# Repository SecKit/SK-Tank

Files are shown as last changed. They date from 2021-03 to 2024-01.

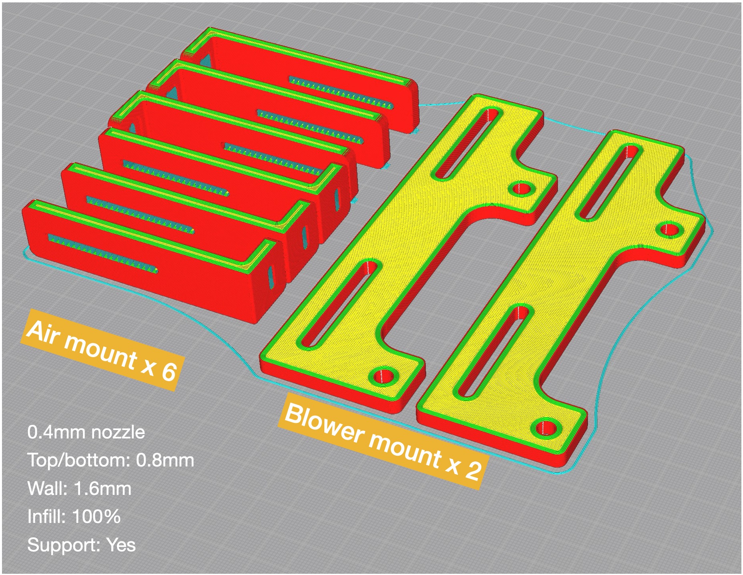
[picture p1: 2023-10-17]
v2/STEP files/must/Side blower ducts/common/slicing tip 1.jpg

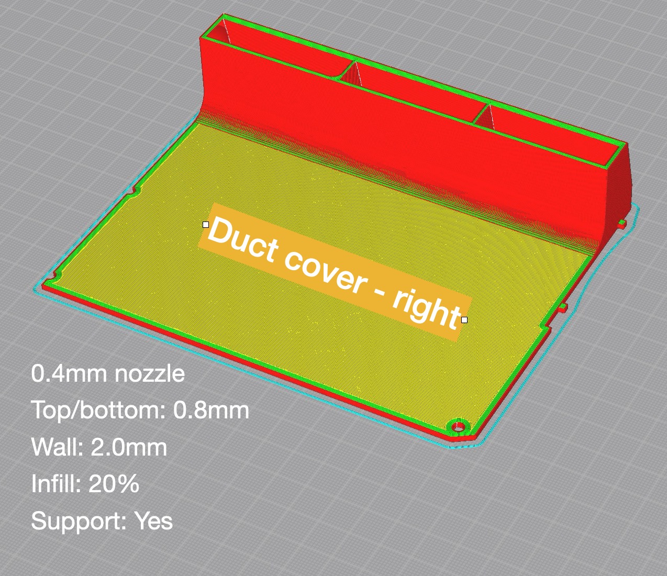
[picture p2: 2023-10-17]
v2/STEP files/must/Side blower ducts/right duct/slicing tip Duct cover - right.jpg

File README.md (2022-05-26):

## SK-Tank All-Metal CoreXY 3D Printer

### Website
https://seckit3dp.design/price/sk-tank

### Wiki: Assembly Manual, tuning guide, etc.
https://sites.google.com/view/seckit-wiki/sk-tank-350x350x400

### Join SecKit's FaceBook group for owner's discussion and latest update
https://www.facebook.com/groups/SecKitCoreXY3DP/

### YouTube
https://www.youtube.com/channel/UCJUHiJfgDE5aeqbk4iZBPHA/videos

### FaceBook Page
https://www.facebook.com/seckit.3dp

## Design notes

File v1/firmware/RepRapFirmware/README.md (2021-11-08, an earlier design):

This firmware pack works on both Mellow Fly CDY v2 and v3 board.

1. Use a max 32G FAT32-format micro SD card. A 64GB or larger card is not supported by Mellow FLY CDY v2 or v3.
2. Extract the zip file and copy all contents in "SK-Tank RRF on Fly CDY v2" directory to the root of a micro SD card.
3. Follow the quick steps in the [Firmware Chapter](https://sites.google.com/view/seckit-wiki/sk-tank-350x350x400/assembly-manual/sk-tank-assembly-manual/12-firmware) of [SK-Tank Assembly Manual](https://sites.google.com/view/seckit-wiki/sk-tank-350x350x400/assembly-manual/sk-tank-assembly-manual) to flash the firmware to your Mellow Fly CDY v2 or v3 control board.

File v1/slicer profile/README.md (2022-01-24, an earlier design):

Thank the community for contributing their settings, but some adjustments can be expected to meet your requirement 😄

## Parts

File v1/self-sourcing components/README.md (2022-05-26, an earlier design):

Self-sourcing components for SK-Tank Barebones Kit.

|Category  |Item | #|Electrical req. |Mechanical req. |
|---|:---|-:|:---|:---|
|Power |Meanwell LRS-200-24 PSU | 1|200 or 350 watt, 24V output |4 holes on back panel (PS.)|
|Power |SSR DC-AC | 1|At least 10 amp AC |2 holes on back panel |
|Power |FS-101 fuse box and fuse | 1|6A for 110V. 3A for 220V. |1 hole on back panel |
|Power |Power switch | 1| | |
|Power |Power cord | 1|At least 0.75 mm^2 internal wire |150cm or longer |
|Control |BigTreeTech Octopus or GTR | 1|At least 6 driver slots |4 holes on back panel |
|Control |TMC2225 | 6|(or other drivers) | |
|Stepper |NEMA17 1.8°/0.9° stepper for XY | 2|Common NEMA 17 stepper | |
|Stepper |NEMA17 1.8° pancake stepper for E | 1|Common NEMA 17 pancake stepper |(PPS.) |
|Extruder  |BMG or Hemera extruder | 1|(PPS.) | |
|Fan |4010 fan for driver cooling | 1|24V | |
|Fan |4020 blower for part cooling | 1|24V | |
|Sensor |Lerdge optical endstop | 3|5V | |
|Sensor |Filament runout sensor | 1|(optional) | |
|Accessory |PTFE tube 3mm ID, 80cm | 1| | |
|Accessory |Cable tie |20| | |
|Accessory |Cable management nylon sleeve, wrapper, etc.| 1| | |

PS. Pre-drilled holes are there on the ACM (Aluminum Composite Material) back panel but you can still drill customized holes easily.

PPS. Use your preferred extruder and design a customized adapter based on [SK-Tank BMG adapter STEP file](https://github.com/SecKit/SK-Tank/tree/master/STEP%20files/extruder%20adapter%20-%20BMG) and [SK-Tank extruder carriage STEP file](https://github.com/SecKit/SK-Tank/tree/master/STEP%20files/extruder%20carriage).

*SecKit will not be responsible for your self-sourcing items.*

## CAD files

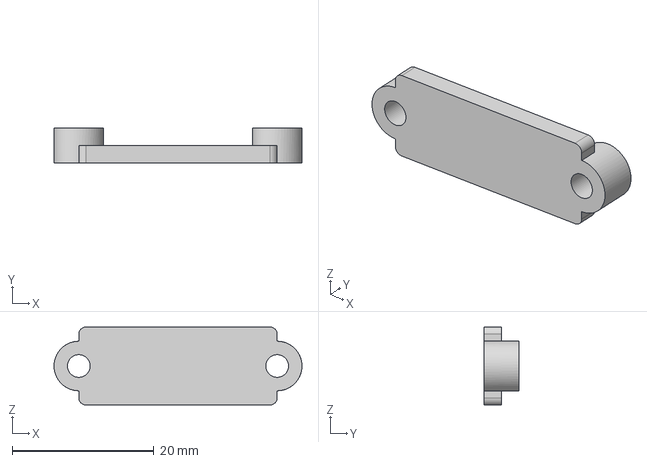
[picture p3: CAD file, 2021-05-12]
STEP files/1. must/Y endstop/Y endstop base.step
35.0 x 5.00 x 11.0 mm

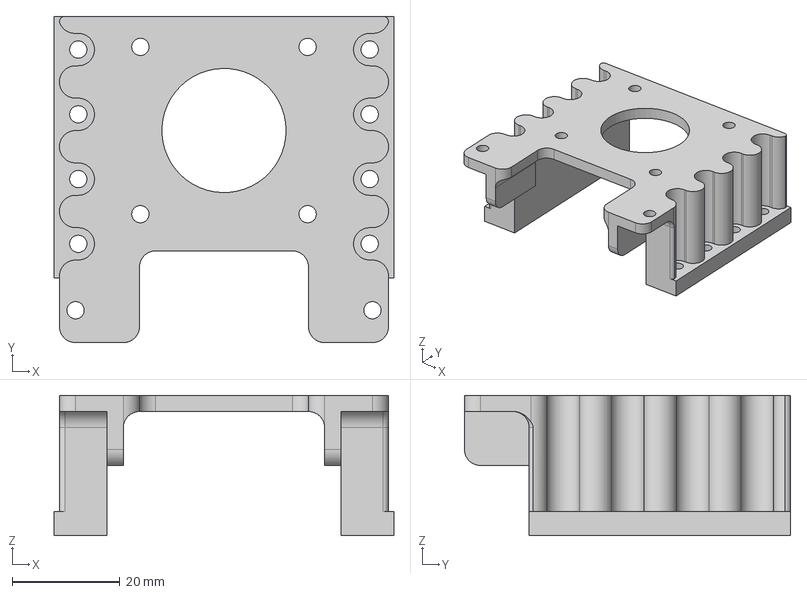
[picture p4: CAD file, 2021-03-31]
STEP files/2. reference/extruder adapter - BMG/SK-Tank BMG printed adapter.step
63.0 x 60.5 x 26.0 mm

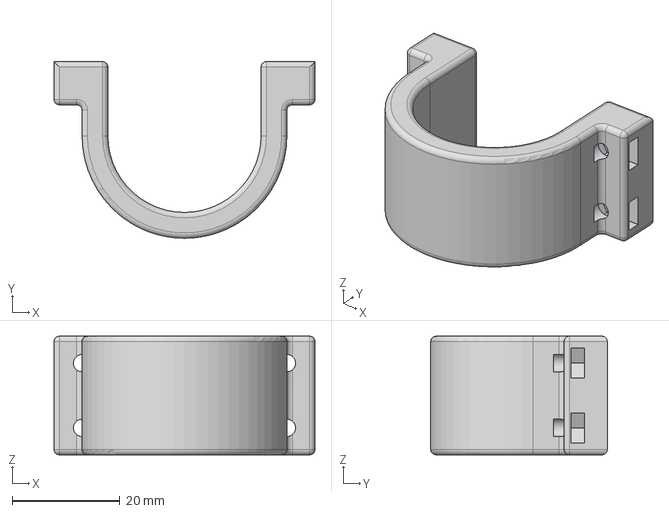
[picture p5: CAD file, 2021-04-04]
STEP files/Belted-Z stepper holder/NEMA8 gearbox bracket.step
48.4 x 32.8 x 22.0 mm

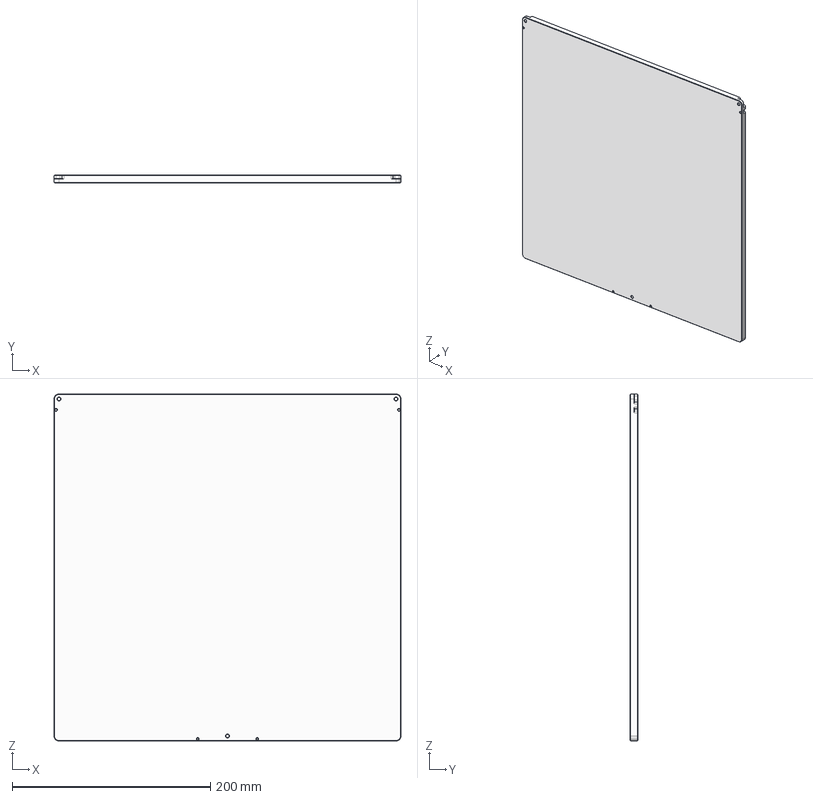
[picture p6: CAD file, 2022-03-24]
STEP files/reference/bed/SK-Tank bed.step
350.0 x 8.00 x 350.0 mm

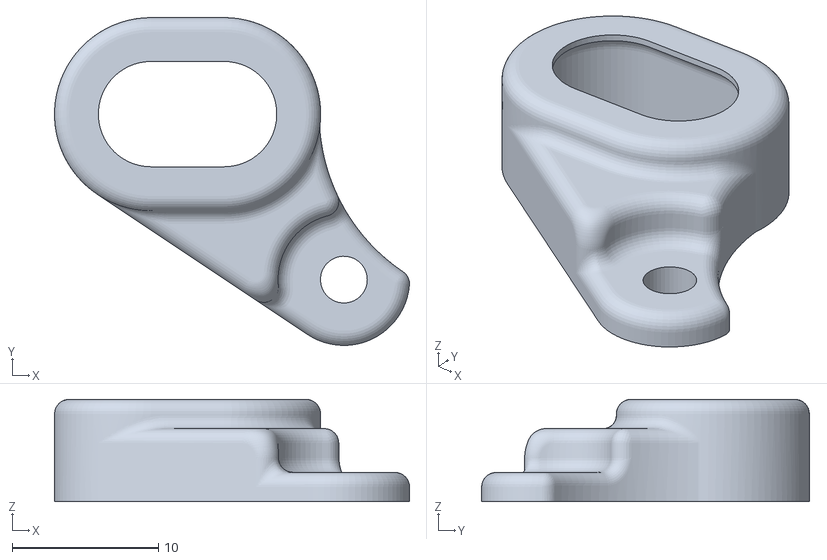
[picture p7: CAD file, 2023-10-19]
v2/STEP files/must/Bed leg guards/right leg guard.stl
24.3 x 22.4 x 7.00

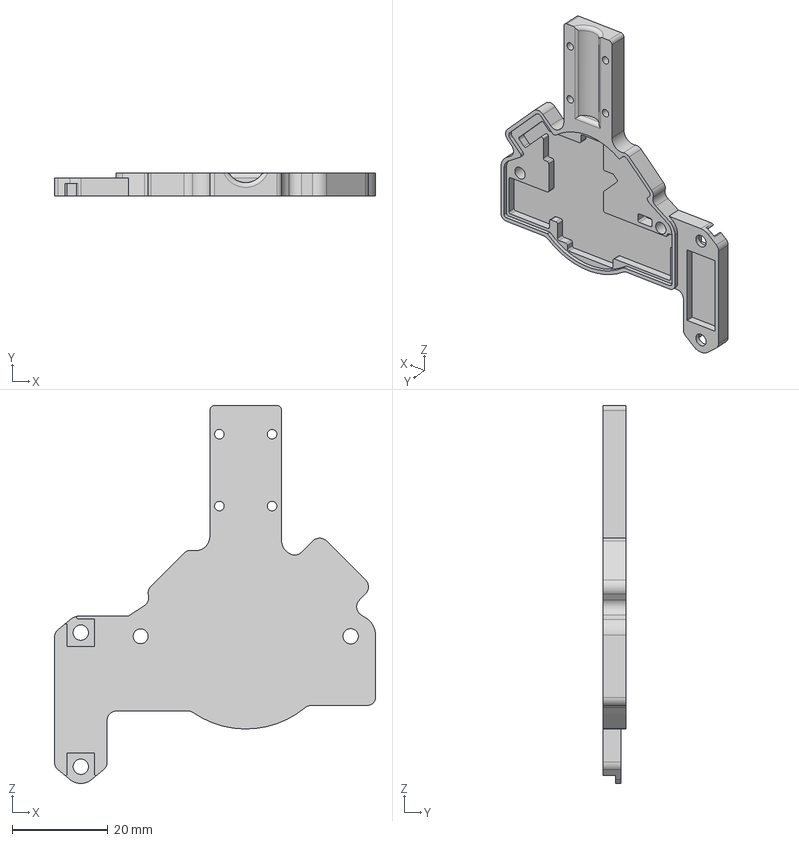
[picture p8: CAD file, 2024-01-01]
v2/STEP files/must/DAB/EBB36 mount/DAB EBB36 mount.step
67.0 x 4.80 x 78.9 mm

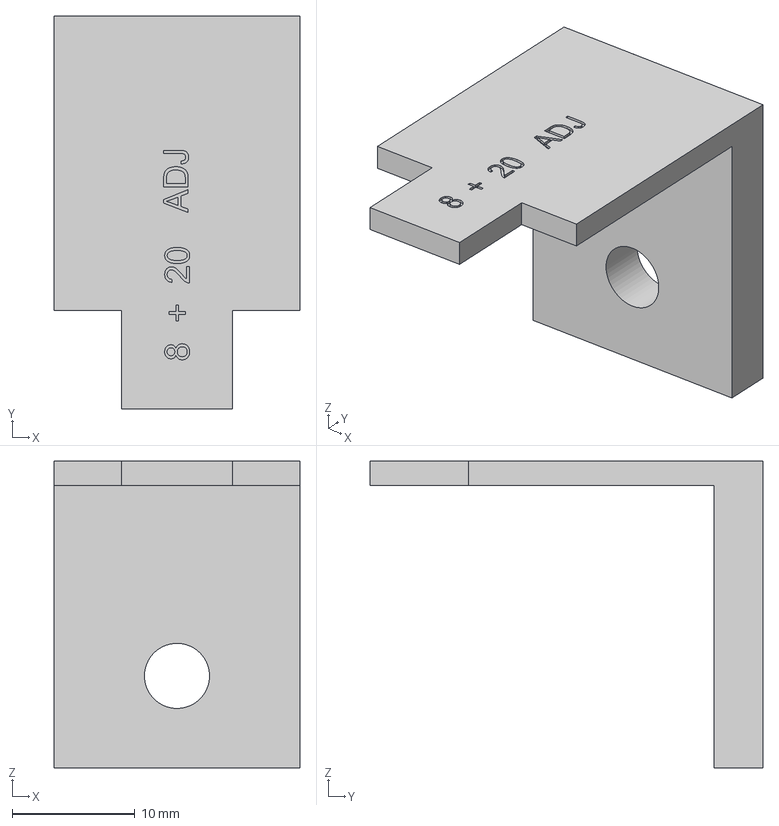
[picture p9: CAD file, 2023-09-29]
v2/STEP files/must/DAB/Fork/DAB fork 8+20 for adjustment.step
20.0 x 32.0 x 25.0 mm

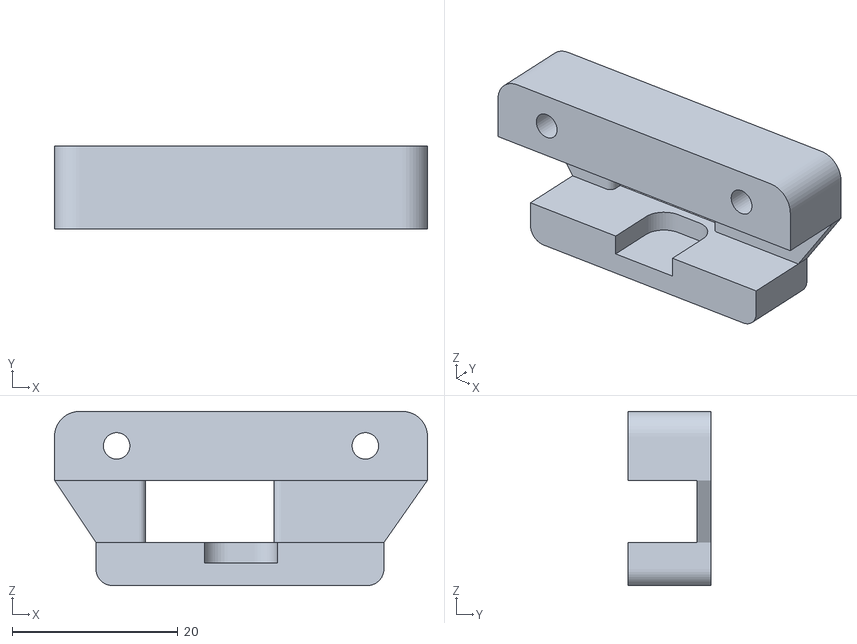
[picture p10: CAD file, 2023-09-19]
v2/STEP files/must/DAB/Latch housing/For MGN12C X linear block/DAB latch housing MGN12C.stl
45.0 x 10.0 x 21.0

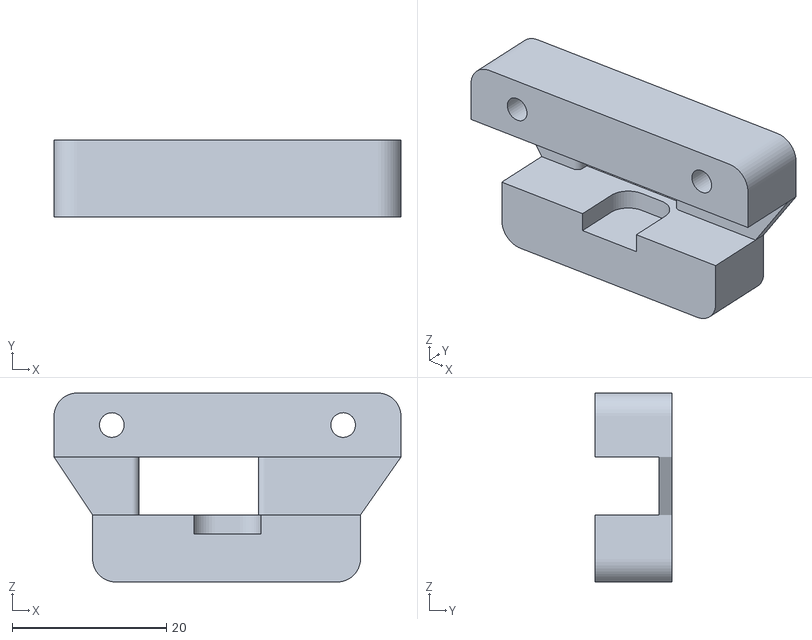
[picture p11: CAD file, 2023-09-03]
v2/STEP files/must/DAB/Latch housing/For MGN9H X linear block/DAB latch housing MGN9H.stl
45.0 x 10.0 x 24.5

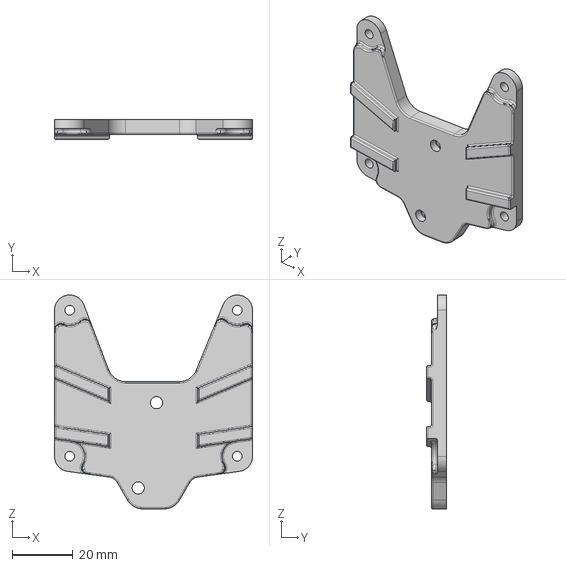
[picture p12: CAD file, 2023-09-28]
v2/STEP files/must/DAB/TBG Air extruder mount/DAB TBG Air extruder mount.step
65.0 x 6.60 x 70.2 mm

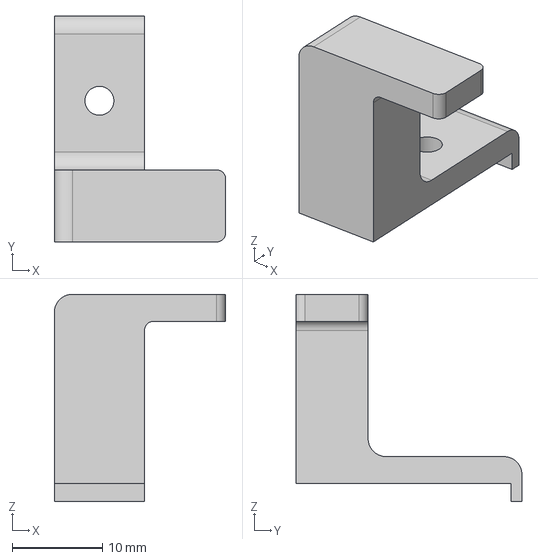
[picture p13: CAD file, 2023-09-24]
v2/STEP files/must/DAB/X endstop finger/DAB X endstop finger.step
19.0 x 25.1 x 23.0 mm

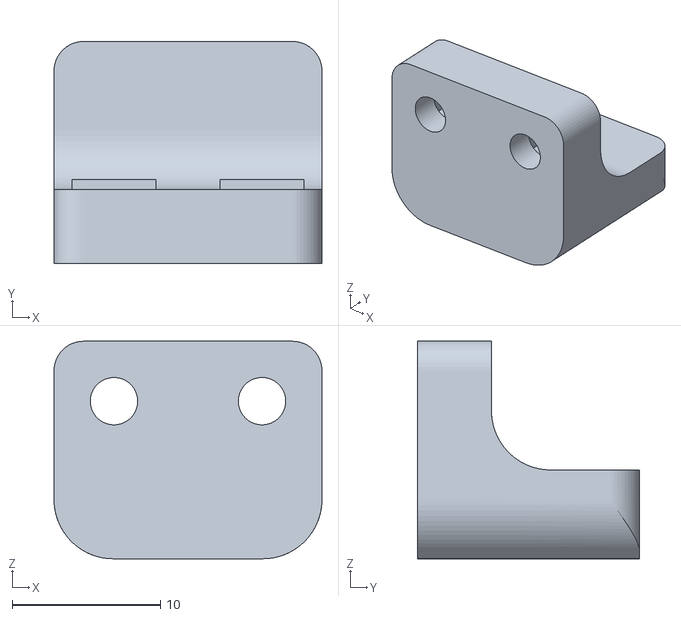
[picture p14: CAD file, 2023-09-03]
v2/STEP files/must/DAB/Z endstop finger/DAB endstop finger.stl
18.1 x 15.0 x 14.7

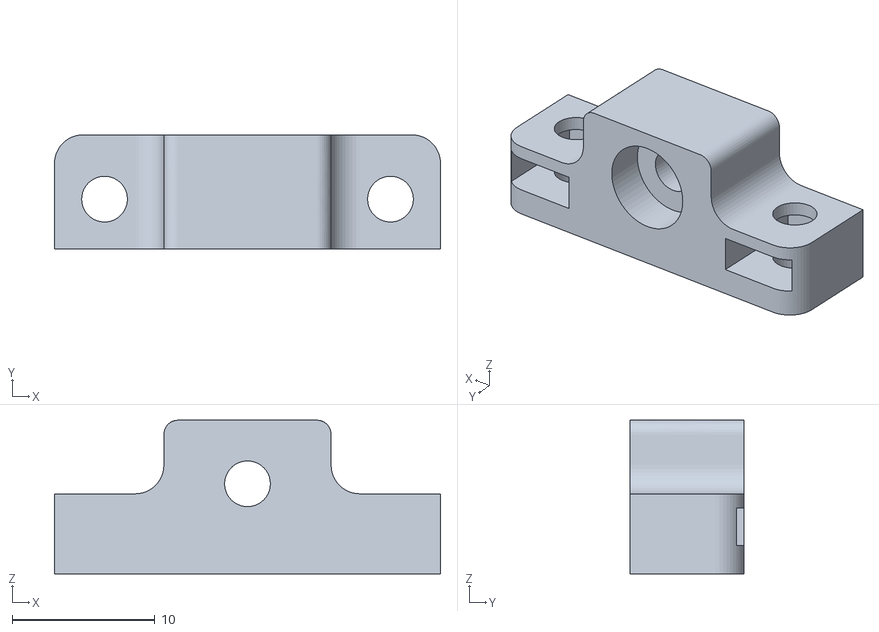
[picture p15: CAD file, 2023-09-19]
v2/STEP files/must/DAB/Z endstop mount/For MGN12C X linear block/DAB Z endstop mount MGN12C.stl
27.0 x 8.00 x 10.8

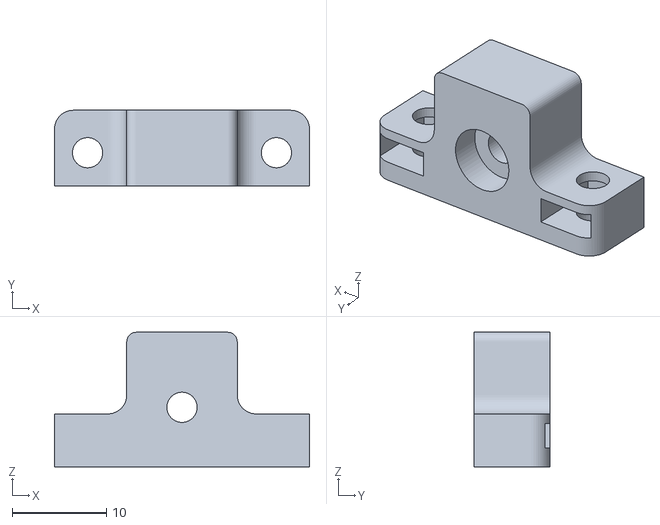
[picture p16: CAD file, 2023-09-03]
v2/STEP files/must/DAB/Z endstop mount/For MGN9H X linear block/DAB Z endstop mount MGN9H.stl
27.0 x 8.00 x 14.2

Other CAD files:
v2/STEP files/must/Grommets/Grommet - toolhead cable.stl
v2/STEP files/must/Side blower ducts/common/activated-carbon basket by Mike Simpson/Basket 3.stl
v2/STEP files/must/Side blower ducts/common/thin tape film.stl
v2/STEP files/must/Side blower ducts/hotend air collector/hotend air collector - right.stl
STEP files/0. assembly tool/m5 nut holder/M5 nut holder.step
STEP files/0. assembly tool/m5 nut holder/M5 nut holder.stl
STEP files/1. must/X endstop/X endstop base.step
STEP files/1. must/X endstop/X endstop base.stl
STEP files/1. must/Y endstop/Y endstop base.stl
STEP files/1. must/Z endstop/Z endstop base.step
STEP files/1. must/Z endstop/Z endstop base.stl
STEP files/1. must/Z endstop/Z endstop finger.step
STEP files/1. must/Z endstop/Z endstop finger.stl
STEP files/1. must/driver cooling fan duct/driver cooling fan duct.step
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

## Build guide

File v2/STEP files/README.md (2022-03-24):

Slicing tips

Printed files are all non-structural components so a common PLA or PETG filament with 0.4mm nozzle and 0.2mm layer height will do. Use ABS/ASA if your printer is enclosed. For special slicing settings please refer to the README.md file and print orientation pictures in each STL directory.   

All designs in this directory and subdirectories are shared under [CC BY-NC-SA 4.0](https://creativecommons.org/licenses/by-nc-sa/4.0/)

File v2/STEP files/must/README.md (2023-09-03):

All printed parts are not structural components so common PLA or PETG with 0.4mm nozzle and 0.2mm layer height will do.

Use ABS if you're going to enclose this printer.

Use **dark color** filament for the endstop fingers or **paint them black** to block the optical sensor.

Slicing settings

|Setting | All |
|:---|:---|
|Quantity |1 |
|Wall thickness |1.6 mm |
|Infill |100% |
|Support |None |

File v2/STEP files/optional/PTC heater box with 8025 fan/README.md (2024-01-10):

Slicer settings

|Setting |Description |
|:---|:---|
|Quantity |1 |
|Wall thickness |2mm |
|Infill |20% |
|Support |Yes |

ABS/ASA, 0.4mm nozzle, 0.2mm layer height

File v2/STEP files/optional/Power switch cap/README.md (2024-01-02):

Slicer settings

|Setting |Description |
|:---|:---|
|Quantity |1 |
|Wall thickness |2mm |
|Infill |100% |
|Support |Yes |

PLA/PETG, 0.4mm nozzle, 0.2mm layer height

Use ABS/ASA if printer is enclosed.

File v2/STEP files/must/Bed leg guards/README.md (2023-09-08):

Slicer settings

|Setting |Description |
|:---|:---|
|Quantity |1 |
|Wall thickness |1.6mm |
|Infill |100% |
|Support |None |

PLA/PETG, 0.4mm nozzle, 0.2mm layer height

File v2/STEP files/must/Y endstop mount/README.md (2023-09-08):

Slicer settings

|Setting |Description |
|:---|:---|
|Quantity |1 |
|Wall thickness |1.6mm |
|Infill |20% or more |
|Support |None |

PLA/PETG, 0.4mm nozzle, 0.2mm layer height

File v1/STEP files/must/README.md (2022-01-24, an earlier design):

All printed parts are not structural components so common PLA or PETG with 0.4mm nozzle and 0.2mm layer height will do.

Use **dark color** filament for the endstop fingers or **paint them black** to block the optical sensor.

Slicing settings

|Setting | Bed retainer | Stpr holder  | Driver duct  | Part cooling | X endstop | Y endstop | Y endstop alt|
|:---|:---|:---|:---|:---|:---|:---|:---|
|Quantity |1 |3 |1 |1 |1 |1 |1 |
|Wall thickness |2  mm |2.8 mm |2 mm |2.8 mm |2.8 mm |2 mm |2 mm |
|Infill |100% |100% |20% |30% |30% |100% |100% |
|Support |None |None |10% |20% w/ blocker|None |None |20% |

Carbon fiber gantry/washers for belt handlers
|Setting | Lower washer | Upper washer |
|:---|:---|:---|
|Quantity |2 |2 |
|Wall thickness |2 mm |2 mm |
|Infill |100% |100% |
|Support |None |None |

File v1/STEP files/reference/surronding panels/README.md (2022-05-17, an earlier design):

Please drill the holes 1~2mm larger for thermal expansion if you're planning to use plastics as panel material. 3mm-thick polycarbonate is recommended. Acrylic will be too crispy. Some foams pasted inside the panels help isolate heat better.

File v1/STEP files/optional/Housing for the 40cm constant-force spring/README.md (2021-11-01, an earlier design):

This spring housing is necessary only for SK-Tank kits sent before 2021 Oct 31st. The constant-force spring acting as a counter-weight at the rear end of the bed is not long enough for the whole Z stroke thus the spring is relocated to bed carriage.

Please slice the spring housing in the orientation as shown in the picture for strength reason.

Slicing tips

|Setting |Description |
|:---|:---|
|Quantity |1 |
|Material |PLA or PETG |
|Wall thickness |2mm and above |
|Infill |100% |
|Support |as shown in the picture |

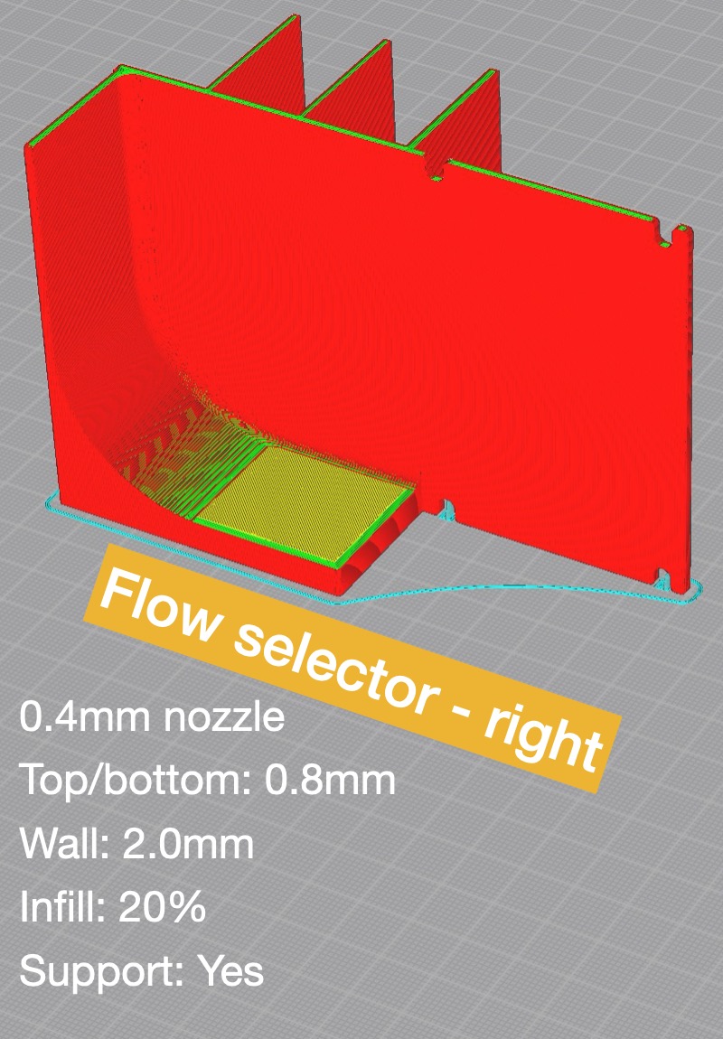
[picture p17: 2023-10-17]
v2/STEP files/must/Side blower ducts/right duct/slicing tip Flow selector - right.jpg

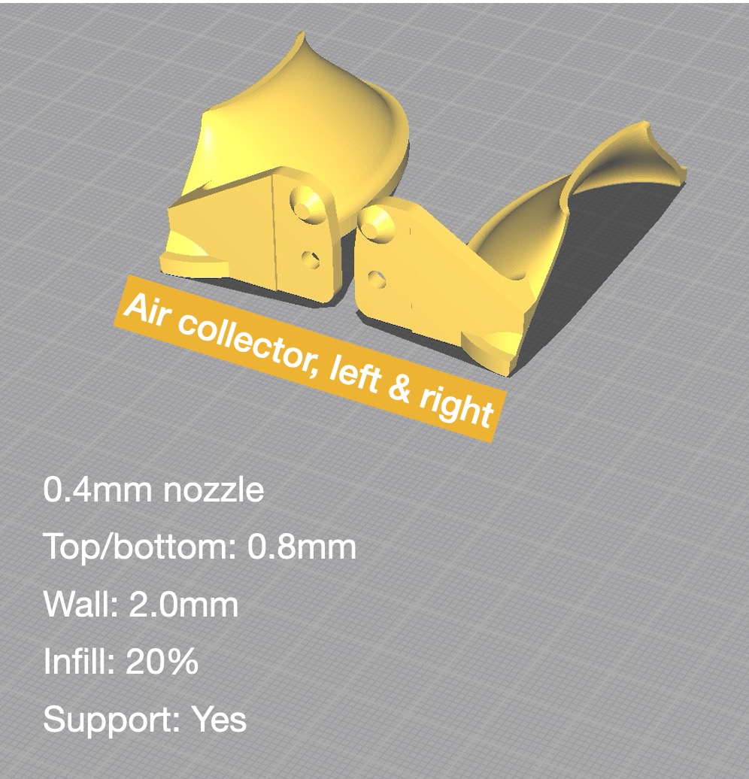
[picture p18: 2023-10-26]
v2/STEP files/must/Side blower ducts/hotend air collector/Slicing tip.jpg

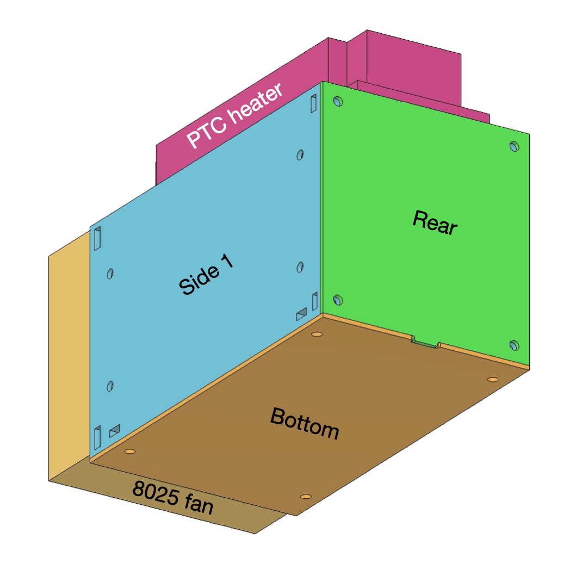
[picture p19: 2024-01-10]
v2/STEP files/optional/PTC heater box with 8025 fan/pic2.jpg

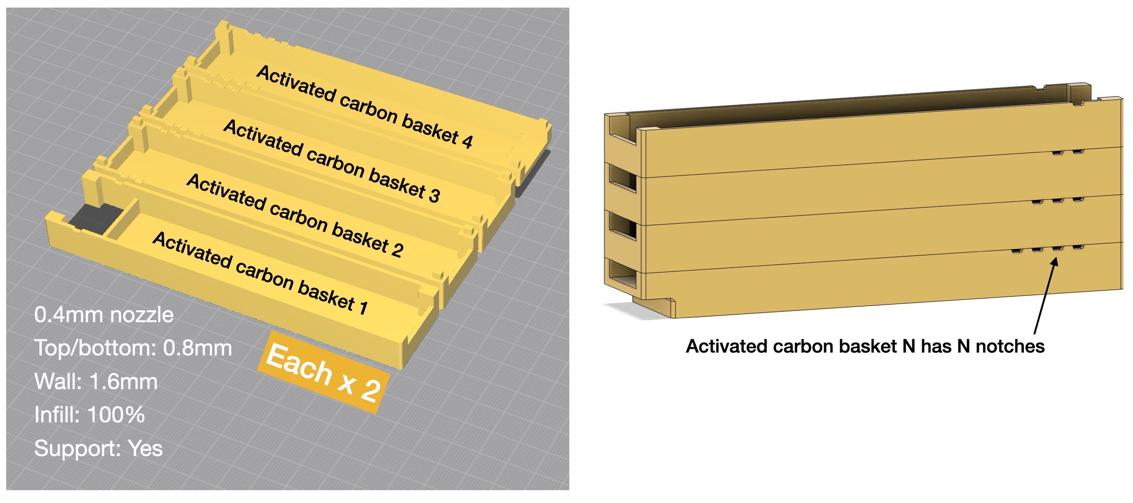
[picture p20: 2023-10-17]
v2/STEP files/must/Side blower ducts/common/slicing tip 2.jpg

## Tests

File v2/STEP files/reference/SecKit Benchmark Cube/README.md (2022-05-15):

## SecKit Benchmark Cube
A 30x30 benchmarking cube to check dimensional accuracy, overhangs, retraction/stringing, ringing, and more.

#### Outer dimension
30x30x30 mm^3

#### Wall thickness
3 mm

#### Overhang angles
- Triangle: 30°
- Hexagon: 30°
- Nonagon: 10°,  50°

#### Gap widths
0.4 mm, 0.3 mm, 0.2 mm, 0.15 mm, 0.1 mm

#### Author
Alan Kilgore, Ernest Lin

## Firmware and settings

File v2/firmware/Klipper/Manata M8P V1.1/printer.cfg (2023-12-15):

# This file can be used as a baseline printer.cfg for the SecKit SK-Tank v2
#####################################################################################
# ATTENTION: Do not use this file without checking and adopting the settings
# according to your actual build! (e.g., wiring, dimensions, extruder setup)
#####################################################################################
# Note: Please check https://www.klipper3d.org/Config_Reference.html for the full
# list of settings. Default settings and those not explicitly set in this cfg file
# can be found there.

########################################
# Basic Settings
########################################

[mcu]
canbus_uuid: ************

[include ebb-canbus-v1.2.cfg]
[include dab.cfg]
[include mainsail.cfg]

[printer]
kinematics: corexy
max_velocity: 500
max_accel: 4000
max_accel_to_decel: 2000
max_z_velocity: 30
max_z_accel: 120

# Note: Extruder settings have to be set on the extruder in the Steppers & Stepper
# Drivers section using "max_extrude_only_velocity:" and "max_extrude_only_accel:" attributes

[virtual_sdcard]
path: ~/printer_data/gcodes

[pause_resume]

[gcode_arcs]
resolution: 0.5

[display_status]

########################################
# Steppers & Stepper Drivers
########################################
# Using TMC2208 configuration for TMC2225 stepper drivers

# Z stepper front left
# Manta M8P V1.1 M1
[stepper_z]
step_pin: PE2
dir_pin: PB4
enable_pin: !PC11
microsteps: 16
rotation_distance: 2 # 4mm of ballscrew 1204 with 1:2 ratio
full_steps_per_rotation: 200 # for a 1.8 stepper
endstop_pin: probe:z_virtual_endstop # use Dab endstop for Z endstop
homing_speed: 12.0
position_min: -10
position_max: 400
homing_retract_dist: 5 # added to lift the nozzle 2mm after homing vs. endstop

# Z1 stepper front right
# Manta MP8 V1.1 M2
[stepper_z1]
step_pin: PF12
dir_pin: PF11
enable_pin: !PB3
microsteps: 16
rotation_distance: 2 # 4mm of ballscrew 1204 with 1:2 ratio
full_steps_per_rotation: 200 # for a 1.8 stepper

# Z2 stepper back center
# Manta MP8 V1.1 M3
[stepper_z2]
step_pin: PD7
dir_pin: PD6
enable_pin: !PF10
microsteps: 16
rotation_distance: 2 # 4mm of ballscrew 1204 with 1:2 ratio
full_steps_per_rotation: 200 # for a 1.8 stepper

# Upper belt stepper right back
# Manta M8P V1.1 M6
[stepper_x]
step_pin: PC9
dir_pin: !PC8
enable_pin: !PD1
microsteps: 16
rotation_distance: 40    # Marlin/RRF reference: 200 steps / mm (rotation_distance = <full_steps_per_rotation> * <microsteps> / <steps_per_mm>)
full_steps_per_rotation: 200 # 400 for a 0.9 stepper
endstop_pin: EBBCan: PB6 ; Manta M8P: PD12
position_endstop: -2.10
position_min: -2.10
position_max: 404.0
homing_speed: 200
homing_retract_dist: 10
second_homing_speed: 50

# Lower belt stepper left back
# Manta MP8 V1.1 M5
[stepper_y]
step_pin: PA10
dir_pin: PA14
enable_pin: !PA15
microsteps: 16
rotation_distance: 40 # Marlin/RRF reference: 200 steps / mm (rotation_distance = <full_steps_per_rotation> * <microsteps> / <steps_per_mm>)
full_steps_per_rotation: 200 # 400 for a 0.9 stepper
endstop_pin: PC1
position_endstop: 410
position_min: -8
position_max: 412
homing_speed: 200
homing_retract_dist: 10
second_homing_speed: 50

# Extruder stepper, using E0 socket
# [extruder]
# # slot 5 --------------
# step_pin: PC13
# dir_pin: PF0
# enable_pin: !PF1
# # slot 6 --------------
# # step_pin: PE2
# # dir_pin: !PE3
# # enable_pin: !PD4
# # slot 7 --------------
# # step_pin: PE6
# # dir_pin: !PA14
# # enable_pin: !PE0
# microsteps: 16
# full_steps_per_rotation: 200
# rotation_distance: 5.7    # LGX Lite
# # rotation_distance: 8.15    # BMG
# # rotation_distance: 4.8     # Orbiter
# nozzle_diameter: 0.400
# filament_diameter: 1.750
# pressure_advance: 0.05    # BMG
# # pressure_advance: 0.075  # Orbiter + Dragon
# sensor_type: ATC Semitec 104GT-2
# heater_pin: PA2 # Heat0
# sensor_pin: PF4 # T0 Header
# #control: pid
# # PID of WM7040 CPAP blower @ 25% speed
# #pid_Kp: 25.108
# #pid_Ki: 0.876
# #pid_Kd: 179.834
# min_extrude_temp: 0
# min_temp: -273
# max_temp: 270
# # PID of dual-4010 blowers
# #pid_Kp: 23.217 # to be adjusted by running PID_CALIBRATE HEATER=extruder TARGET=210
# #pid_Ki: 1.080 # to be adjusted by running PID_CALIBRATE HEATER=extruder TARGET=210
# #pid_Kd: 124.502  # to be adjusted by running PID_CALIBRATE HEATER=extruder TARGET=210

[verify_heater extruder]
hysteresis: 10

########################################
# TMC2208 Configuration
########################################

[tmc2208 stepper_x]
uart_pin: PF8
interpolate: True
run_current: 0.95
#hold_current: 0.400
sense_resistor: 0.110
stealthchop_threshold: 0   # mm/s
# stealthchop_threshold: 999999
# driver_IHOLDDELAY: 8        # Default 8
# driver_TPOWERDOWN: 20       # Default 20
# driver_TBL: 1               # Default 2
# driver_TOFF: 2              # Default 3
# driver_HEND: 1              # Default 0
# driver_HSTRT: 7             # Default 5
# driver_PWM_AUTOGRAD: False  # Default True
# driver_PWM_AUTOSCALE: False # Default True
# driver_PWM_LIM: 12          # Default 12
# driver_PWM_REG: 8           # Default 8
# driver_PWM_FREQ: 2          # Default 1
# driver_PWM_GRAD: 18         # Default 14
# driver_PWM_OFS: 36

[tmc2208 stepper_y]
uart_pin: PD0
interpolate: True
run_current: 0.95
#hold_current: 0.40
sense_resistor: 0.110
stealthchop_threshold: 0   # mm/s
# stealthchop_threshold: 999999
# driver_IHOLDDELAY: 8        # Default 8
# driver_TPOWERDOWN: 20       # Default 20
# driver_TBL: 1               # Default 2
# driver_TOFF: 2              # Default 3
# driver_HEND: 1              # Default 0
# driver_HSTRT: 7             # Default 5
# driver_PWM_AUTOGRAD: False  # Default True
# driver_PWM_AUTOSCALE: False # Default True
# driver_PWM_LIM: 12          # Default 12
# driver_PWM_REG: 8           # Default 8
# driver_PWM_FREQ: 2          # Default 1
# driver_PWM_GRAD: 18         # Default 14
# driver_PWM_OFS: 36

[tmc2208 stepper_z]
uart_pin: PC10
interpolate: True
run_current: 0.40
hold_current: 0.300

[tmc2208 stepper_z1]
uart_pin: PF13
interpolate: True
run_current: 0.40
hold_current: 0.300

[tmc2208 stepper_z2]
uart_pin: PF9
interpolate: True
run_current: 0.40
hold_current: 0.300

# [tmc2208 extruder]
# uart_pin: PE4
# interpolate: True
# run_current: 0.90      # BMG
# # run_current: 0.350    # Orbiter
# hold_current: 0.250
# stealthchop_threshold: 0   # mm/s

########################################
# Bed Heaters & Fans
########################################

# Manta M8P V1.1 BED-OUT
[heater_bed]
heater_pin: PB7
sensor_pin: PA0 # BED
sensor_type: Generic 3950
control = pid       # changed to "watermark" and comment/delete the PID settings below if you have issues with the SSR (like some SSR don't like PID control)
pid_Kp = 67.029     # CF build plate. PID_CALIBRATE HEATER=heater_bed TARGET=60
pid_Ki = 1.752      # CF build plate. PID_CALIBRATE HEATER=heater_bed TARGET=60
pid_Kd = 640.963    # CF build plate. PID_CALIBRATE HEATER=heater_bed TARGET=60
min_temp: -100
max_temp: 130

# [fan]
# pin: PA8 # FAN0

# [heater_fan fan1]
# pin: PE5 # FAN1

# [heater_fan fan2]
# pin: PC8 # FAN2

# [controller_fan xy_driver_fan]
# pin: PC8 # FAN2
# heater: extruder
# stepper: stepper_x,stepper_y
# idle_timeout: 30

[temperature_sensor mcu_temp]
sensor_type: temperature_mcu

# Manta M8P V1.1 HE2
[output_pin blower_left]
pin: PB6
scale: 255
shutdown_value: 0.0
pwm: True
cycle_time: 0.05
# The default cycle_time 0.01 might generate noise at low fan speed value.
# Choose a value which you can bear with the noise, usually between 0.005 and 0.5.

# Manta M8P V1.1 HE3
[output_pin blower_right]
pin: PE1
scale: 255
shutdown_value: 0.0
pwm: True
cycle_time: 0.05
# The default cycle_time 0.01 might generate noise at low fan speed value.
# Choose a value which you can bear with the noise, usually between 0.005 and 0.5.

[gcode_macro M106]
rename_existing:
    M106
gcode:
    {% if params.P is defined %}
      {% if params.S is defined %}
        SET_PIN PIN=fan{params.P|int} VALUE={params.S|int}
      {% else %}
        SET_PIN PIN=fan{params.P|int} VALUE=255
      {% endif %}
    {% else %}
      {% if params.S is defined %}
        SET_PIN PIN=blower_left VALUE={params.S|int}
        SET_PIN PIN=blower_right VALUE={params.S|int}
      {% else %}
        SET_PIN PIN=blower_left VALUE=255        
        SET_PIN PIN=blower_right VALUE=255
      {% endif %}
    {% endif %}

[gcode_macro M107]
rename_existing:
    M107
gcode:
    {% if params.P is defined %}
      SET_PIN PIN=fan{params.P|int} VALUE=0      
    {% else %}
      SET_PIN PIN=blower_left VALUE=0
      SET_PIN PIN=blower_right VALUE=0      
    {% endif %}
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

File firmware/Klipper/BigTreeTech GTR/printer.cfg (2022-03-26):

# This file contains common pin mappings for the 6 stepper motor
# "BigTreeTech GTR" board. To use this config, the firmware should
# be compiled for the STM32F407 with a "32KiB bootloader".
# see hardware details on https://github.com/bigtreetech/BIGTREETECH-GTR-V1.0

# The "make flash" command does not work on the GTR. Instead,
# after running "make", copy the generated "out/klipper.bin" file to a
# file named "firmware.bin" on an SD card and then restart the GTR
# with that SD card.

# See docs/Config_Reference.md for a description of parameters.


# This file can be used as a basline printer.cfg for the SecKit SK-Tank 
#####################################################################################
# ATTENTION # You shall not use this file without checking and adopting the settings
# according to your actual built! (e.g. wiring, dimensions, extruder setup) #
#####################################################################################
# Note: please check https://www.klipper3d.org/Config_Reference.html to get the full
# list of settings. Default settings and not set explicit in this cfg


########################################
# basic settings
########################################

[mcu]
restart_method: command
serial: /dev/serial/by-id/usb-Klipper_stm32f407xx_37003A000647393430363638-if00
#serial: /dev/ttyACM0

[printer]
kinematics: corexy
max_velocity: 300
max_accel: 3000     ; it was 2000. set to 7000 for resonance test
max_accel_to_decel: 3000
max_z_velocity: 7
max_z_accel: 100
# Note: Extruder settings have to be set in on the extruder in the Steppers & Stepper 
# Drivers section usig "max_extrude_only_velocity:" and "max_extrude_only_accel:" attributes

########################################
# Steppers & Stepper Drivers
########################################
# using TMC2208 configuration for TMC2225 steper drivers

# lower belt stepper left back
[stepper_x]
step_pin: PC15
dir_pin: PF0        # for standard SK-Tank wiring you have to change the direction by adding "!" so the new pin will be "!PF0"
enable_pin: !PF1
microsteps: 16
rotation_distance: 32    # Marlin/RRF reference: 200 steps / mm (rotation_distance = <full_steps_per_rotation> * <microsteps> / <steps_per_mm>)
full_steps_per_rotation:400 # for a 0.9 stepper
endstop_pin: ^PF2
position_endstop: 0
position_max: 344
homing_speed: 150

# upper belt stepper right back
[stepper_y]
step_pin: PE3
dir_pin: PE2
enable_pin: !PE4
microsteps: 16
rotation_distance: 32 # Marlin/RRF reference: 200 steps / mm (rotation_distance = <full_steps_per_rotation> * <microsteps> / <steps_per_mm>)
full_steps_per_rotation:400 # for a 0.9 stepper
endstop_pin: ^PC13
position_endstop: 0
position_max: 345
homing_speed: 150

# Z stepper front left
[stepper_z]
step_pin: PB8
dir_pin: PB7
enable_pin: !PB9
microsteps: 16
rotation_distance: 32 # Marlin/RRF reference: 2000 steps / mm (rotation_distance = <full_steps_per_rotation> * <microsteps> / <steps_per_mm> * <gear_ratio>)
full_steps_per_rotation:200 # for a 1.8 stepper
gear_ratio: 20:1 # to match z stepper 20:1 gearbox NEMA8
endstop_pin: probe:z_virtual_endstop # use optical endstop for Z endstop
position_min: -5
position_max: 400
homing_retract_dist: 2 # added to lift the nozzel 2mm after homing vs. endstop

# Z1 stepper front right, using E1 socket
[stepper_z1]
step_pin: PD6
dir_pin: !PD5
enable_pin: !PD7
microsteps: 16
rotation_distance: 32 # Marlin/RRF reference: 2000 steps / mm (rotation_distance = <full_steps_per_rotation> * <microsteps> / <steps_per_mm> * <gear_ratio>)
full_steps_per_rotation:200 # for a 1.8 stepper
gear_ratio: 20:1 # to match z stepper 20:1 gearbox NEMA8

# Z2 stepper back center, using E2 socket
[stepper_z2]
step_pin: PD1
dir_pin: PD0
enable_pin: !PD2
microsteps: 16
rotation_distance: 32 # Marlin/RRF reference: 2000 steps / mm (rotation_distance = <full_steps_per_rotation> * <microsteps> / <steps_per_mm> * <gear_ratio>)
full_steps_per_rotation:200 # for a 1.8 stepper
gear_ratio: 20:1 # to match z stepper 20:1 gearbox NEMA8

# extruder stepper, using E0 socket
[extruder]
step_pin: PG12
dir_pin: PG11
enable_pin: !PG13
microsteps: 16
full_steps_per_rotation: 200
rotation_distance: 8.15
nozzle_diameter: 0.400
filament_diameter: 1.750
pressure_advance: 0.05
sensor_type: ATC Semitec 104GT-2
heater_pin: PB1 # Heat0
sensor_pin: PC1 # T0 Header
control: pid
pid_Kp: 23.217 # to be adjusted by running PID_CALIBRATE HEATER=extruder TARGET=210
pid_Ki: 1.080 # to be adjusted by running PID_CALIBRATE HEATER=extruder TARGET=210
pid_Kd: 124.502  # to be adjusted by running PID_CALIBRATE HEATER=extruder TARGET=210
min_extrude_temp: 190
min_temp: 0
max_temp: 250



########################################
# TMC2208 configuration
########################################

[tmc2208 stepper_x]
uart_pin: PC14
interpolate: True
run_current: 0.700
hold_current: 0.500
#stealthchop_threshold: 50   # Speed in mm/s. Enable this if you need constantly low movement and found undesired noise around 45mm/s

[tmc2208 stepper_y]
uart_pin: PE1
interpolate: True
run_current: 0.700
hold_current: 0.500
#stealthchop_threshold: 50   # Speed in mm/s. Enable this if you need constantly low movement and found undesired noise around 45mm/s

[tmc2208 stepper_z]
uart_pin: PB5
interpolate: True
run_current: 0.500
hold_current: 0.400

[tmc2208 extruder]
uart_pin: PG10
interpolate: True
run_current: 0.700
hold_current: 0.300

[tmc2208 stepper_z1]
uart_pin: PD4
interpolate: True
run_current: 0.500
hold_current: 0.400

[tmc2208 stepper_z2]
uart_pin: PC12
interpolate: True
run_current: 0.500
hold_current: 0.400

########################################
# BED HEATERS & FANS
########################################

[heater_bed]
heater_pin: PA2
sensor_pin: PC0 # BED
sensor_type: Generic 3950
control = pid       # changed to "watermark" and comment/delete the PID seetings below if you have issues with the SSR (like some SSR dont like PID control)
pid_kp = 67.500     # to be adjusted by running PID_CALIBRATE HEATER=heater_bed TARGET=60
pid_ki = 1.948      # to be adjusted by running PID_CALIBRATE HEATER=heater_bed TARGET=60
pid_kd = 584.715    # to be adjusted by running PID_CALIBRATE HEATER=heater_bed TARGET=60
min_temp: 0
max_temp: 80

[fan]
pin: PE5 # FAN0

[heater_fan fan1]
pin: PE6 # FAN1

#[heater_fan fan2]
#pin: PC8 # FAN2

[controller_fan xy_driver_fan]
pin: PC8 # FAN2
heater: extruder
stepper: stepper_x,stepper_y
idle_timeout: 30

[temperature_sensor mcu_temp]
sensor_type: temperature_mcu

#[temperature_sensor k_therm]
#sensor_type: MAX31855
#sensor_pin: PH9
#spi_bus: spi2b



########################################
# Inductive sensor
########################################

[probe]
pin: ^PE0
x_offset: -23.0
y_offset: 14.0
#z_offset: 1.2
speed: 7.5  #   Speed (in mm/s) of the Z axis when probing. The default is 5mm/s.
samples: 1


########################################
# BL-Touch
########################################
#[bltouch]
#sensor_pin: ###
#control_pin: ###
#pin_move_time: 0.4
#stow_on_each_sample: True
#probe_with_touch_mode: True #Needed for BLTouch V3.0 / V3.1
#x_offset: -26.0
#y_offset: 0.0
#z_offset: 2.65
#speed: 5
#samples: 2
#sample_retract_dist: 2
#samples_result: average

[safe_z_home]
home_xy_position: 175,175 # Change coordinates to the center of your print bed
speed: 150
z_hop: 10                 # Move up 10mm
z_hop_speed: 7.5

[bed_mesh]
speed: 150
horizontal_move_z: 3
mesh_min: 10,20         # coord of the probe acting a nozzle, so the coord of nozzle will be shifted
mesh_max: 300,310       # coord of the probe acting a nozzle, so the coord of nozzle will be shifted
probe_count: 7,7
algorithm: bicubic
bicubic_tension: 0.2
move_check_distance: 5
split_delta_z: .025
fade_start: 1
fade_end: 10
#fade_target: 0

[z_tilt]
z_positions:
	0, 6
	340, 6
    175, 350
points:
	20, 5
	330, 5
    175, 310
speed: 200
horizontal_move_z: 15
#retries: 1
#retry_tolerance: 0.1

[force_move]
enable_force_move: True #   Set to true to enable FORCE_MOVE and SET_KINEMATIC_POSITION

########################################
# Resonance compensation
########################################

# [mcu rpi]
# serial: /tmp/klipper_host_mcu

# [adxl345]
# cs_pin: rpi:None

# [resonance_tester]
# accel_chip: adxl345
# probe_points: 175,175,20  # at the center of bed


########################################
# Filament Switch Sensor
########################################

#[filament_switch_sensor my_sensor]
#pause_on_runout: True
#switch_pin: ^!PC6 # X-Max pin


######################################################################
# Plug pin locations
######################################################################
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

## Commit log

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2021-04-04 add STEP files of Belted-Z gearbox stepper mount
    [NEMA8 gearbox bracket.step, NEMA8 gearbox bracket.stl]
2021-04-04 add STEP & STL of the driver cooling fan duct and the m5 nut holder
    [M5 nut holder.step, M5 nut holder.stl, driver cooling fan duct.step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]
2021-04-18 Correct the limitation on extruder stepper.
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2021-05-16 update link to SK-Go part cooling fan duct
    [M5 nut holder.step, M5 nut holder.stl, NEMA8 gearbox bracket.step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]
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2021-05-21 Update fan duct with inductive ABL sensor mount
    [SK-Go fan duct v2 + E3D V6 hotend + inductive ABL.stl, SK-Go fan duct v2 + E3D v6 hotend + inductive ABL.step, SK-Go fan duct v2 + Volcano hotend + inductive A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]
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2021-05-24 upload STL of 2GT 10mm belt clamp for XY belts
    [2GT 10mm XY belt clamp.step, 2GT 10mm XY belt clamp.stl]
2021-05-24 add a link of how to setup inductive ABL sensor in bed.g
    [bed.g]
2021-05-24 Add Y-Max stopper block designed by Laurens F.
    [y-max stopper block.stl]
2021-05-25 Upload a zip file of the SD contents for Fly CDY v2 board.
    [bed.g, config.g, homeall.g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]
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2021-05-27 rename directory and remind to print 3 holders
    [NEMA8 gearbox bracket.step, NEMA8 gearbox bracket.stl]
2021-05-27 Add M561 at the beginning of bed.g, and upload all files from extracted from the zip.
    [bed.g, config.g, heightmap.csv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]
2021-06-07 Add end script: optionally move the bed to the bottom after print to prevent falling with stepper disabled.
2021-06-09 Reverse XY stepper direction in config.g
    [config.g]
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2021-06-13 Configure filament sensor in config.g. Disabled by default for owners to confirm the polarity at sensor side.
    [config.g]
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2021-07-03 To prevent confusion, comment out the G31 in config.g as another G31s are in bed.g.
    [config.g]
2021-07-05 Remove the parameter P of M558 in bed.g as it resets the probe offsets assigned in G31. The probe offsets are now assigned once in config.g at boot time.
    [bed.g, config.g]
2021-07-07 Raise the Y & Z endstop 1.5mm for their fingers to trigger more easily.
    [Y endstop base.step, Y endstop base.stl, Z endstop base.step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]
2021-07-08 Replace the Y endstop base with rotation-proof ones
    [Y endstop base - alt.step, Y endstop base - alt.stl, Y endstop base - default.step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]
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2021-07-09 Make the hole deeper 1 mm for an M3 x 8 bolt
    [X endstop base.step, X endstop base.stl]
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2021-07-25 Extend the air ducts so both air nozzles can be closer to filament nozzle.
    [SK-Go fan duct v2 + Volcano hotend + inductive ABL.step, SK-Go fan duct v2 + Volcano hotend + inductive ABL.stl]
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2021-07-31 reduce max E speed from 100mm/s to 40mm/s to prevent step skipping.
    [config.g]
2021-08-01 retract & extrude less during pause.g & resume.g. It was 10mm which clogs the nozzle easily. It's now less than 1mm. In Cura profile, set the default retraction 0.4mm & 50mm/s. In config.g, set max e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
    [config.g, pause.g, resume.g]
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2021-08-05 home XY more slowly to prevent hard collision
    [homex.g, homey.g]
2021-08-05 adjust distance of retraction before pause and extrude after resume to reduce Volcano clogging with PLA
    [pause.g, resume.g]
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2021-08-05 Move Z endstop printed files to the optional components directory as by default the inductive sensor acts as both Z endstop and ABL sensor.
    [Z endstop base.step, Z endstop base.stl, Z endstop finger.step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]
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2021-09-15 minor change to avoid interference
    [SK-Go 4010 part cooling duct.step, SK-Go 4010 part cooling duct.stl]
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2021-09-19 correct mounting hole positions so the air nozzles are lower for SK-Go
    [SK-Go 4010 part cooling duct.step, SK-Go 4010 part cooling duct.stl]
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2021-09-20 correct BLTouch trigger height
    [SK-Go BLTouch mount.step, SK-Go BLTouch mount.stl, SK-Tank BLTouch mount.step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]
2021-09-20 correct the entry of top front m3 nut for the left 4010 blower
    [SK-Go 4010 part cooling duct.step, SK-Go 4010 part cooling duct.stl, SK-Tank 4010 part cooling duct.step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]
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2021-10-06 Shrink the nut hole a little bit to hold the nut better
    [M5 nut holder.3mf, M5 nut holder.step, M5 nut holder.stl]
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2021-10-15 add a distributer in the right air duct to even the air flow by 4010 blower
    [SK-Go 4010 part cooling duct.3mf, SK-Go 4010 part cooling duct.step, SK-Go 4010 part cooling duct.stl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]
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2021-10-19 restore the wrong file name
    [SK-Tank inductive sensor mount.stl]
2021-11-01 add a temporary spring housing for the short 40cm static-force spring
    [hole template.3mf, hole template.step, spring housing.3mf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]
2021-11-01 correct a typo
    [hole template.3mf, hole template.step, spring housing.3mf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]
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2022-02-10 rename bed heater temperature sensor to "Generic 3950" and remove deprecated "default_parameter_xxx" parameters.
    [printer.cfg]
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2022-02-13 bug fix
    [printer.cfg]
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2022-03-24 Bug fix: close the gap between the separator and rear wall.
    [SK-Go fan duct v2 + E3D V6 hotend + inductive ABL.stl, SK-Go fan duct v2 + E3D v6 hotend + inductive ABL.step, SK-Go fan duct v2 + Volcano hotend + inductive A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]
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2022-03-26 correct a typo of duplicated "sensor_type"
    [printer.cfg]
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2022-05-09 add the design of SK-Tank bed in 2 sizes: 350 and 355
    [SK-Tank bed 350x350x6.step, SK-Tank bed 350x350x8.step, SK-Tank bed 355x355x6.step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]
2022-05-13 Added printer.cfg and euclid.cfg for my current setup using the Euclid probe
    [tank-octopus-pro-klipper-mainsail-euclid_euclid.cfg, tank-octopus-pro-klipper-mainsail-euclid_printer.cfg]
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2022-11-24 Lower the default max XY moving speed to 350mm/s or 21000mm/min based on the max 1000 RPM of MKS Servo42C.
    [OctopusV1.1_Klipper_SKGo_TripleZ_BLTouch_Servo42C.cfg, config.g]
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2023-09-19 Move the Y endstop toward inner side of the printer to leave more space between endstop bolts and the frame.
    [Y endstop finger.step, Y endstop finger.stl, Y endstop mount.step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]
2023-09-19 Move latch housing and Z endstop mount to the MGN9H specific directory.
    [DAB endstop finger.stl, DAB endstop mount.stl, DAB latch housing.stl]
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2023-09-21 add bed leg guards to prevent bed from falling
    [left leg guard.stl, right leg guard.stl]
2023-09-23 Extend the X endstop finger so it can trigger the optical endstop
    [DAB X endstop finger.step, DAB X endstop finger.stl, X endstop finger - non-DAB.step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]
2023-09-24 Further extend the X endstop finger so it can trigger the optical endsop
    [DAB X endstop finger.step, DAB X endstop finger.stl, X endstop finger - non-DAB.step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]
2023-09-24 fix a dimension bug
    [X endstop finger - non-DAB.step, X endstop finger - non-DAB.stl]
2023-09-27 add Klipper cfg file templates. Coordinate related params need to be tuned.
    [dab.cfg, ebb-canbus-v1.2.cfg, printer.cfg]
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2023-10-17 missing square nut entry in the air boxes and missing fillets in the covers
    [Air box - left.stl, Air box - right.stl, Duct cover - right.stl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]
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2023-10-18 set a cycle_time value to lower the noise at low blower speeds.
    [printer.cfg]
2023-10-19 add stronger printed Z top brackets to replace the folded sheet metal ones.
    [Z top bracket - front.step, Z top bracket - front.stl, Z top bracket - rear.step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]
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2023-10-24 Use nuts to replace latches for better structure strength
    [Air box - left.stl, Air box - right.stl, Duct cover - left.stl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]
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2023-11-03 Exchange the driver slots of XY steppers to adapt Tank v2 CoreXY belt routing
    [printer.cfg]
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2023-11-14 Bug fix: one belt hole was offset by 1mm
    [extruder carriage.step]
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2023-11-15 lower the max_z_velocity from 50 to 30 mm/s to avoid overload and errorous z movement.
    [printer.cfg]
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2023-12-02 Replace the baskets with Mike Simpson's design which is easier to be printed.
    [Basket 1 Top.stl, Basket 2.stl, Basket 3.stl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]
2023-12-08 Upload the front PC panel DXF for 4-stepper setup designed by Mike Simpson
    [T_ENCL_TOP_NEMA17_48mm_by Mike_Simpson.dxf]
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2023-12-21 bug fix: correct the position of the left stepper hole.
    [T_ENCL_TOP_NEMA17_48mm_by Mike_Simpson.dxf]
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2024-01-10 Upload a new PTC heater box using a 8025 fan. This allows the PTC heater to be fully powered (100% duty cycle).
    [PTC heater box 8025 fan - bottom.stl, PTC heater box 8025 fan - rear.stl, PTC heater box 8025 fan - side1.stl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]
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2024-03-27 Move the front upper PC panel to the 4.0mm directory. Update the top panel for Mike's Dome design.
    [T_ENCL_FRONT_UP_NEMA17_48mm_by Mike_Simpson.dxf, T_ENCL_TOP.dxf]
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
